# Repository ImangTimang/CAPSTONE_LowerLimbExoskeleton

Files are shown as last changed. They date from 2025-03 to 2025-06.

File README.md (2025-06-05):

# Development of a Lower Body Exoskeleton Robot

## Disclaimer
 All published here are the raw files and compilations of the drawings, schematics, programs, and design of the MEXE Capstone 1 and 2 entitled "Development of a Lower Body Exoskeleton Robot"

## Abstract
Lower-limb exoskeletons are wearable robotic systems designed to assist individuals with impairedmobility. As studies in the University solely focused on models and simulations of the lower limb. This capstone
project aims to address the gap by developing a functional prototype of a lower-body exoskeleton robot, limited on sitting and standing postures. SOLIDWORKS were used in analyzing the Adia et. al. (2022) exoskeleton
design for mechanical modeling. Design Calculations were presented by identifying the intended user’s weight and height, material selected upon the main frame and straps, Degrees of Freedom (DOF), recommended size of batteries, and gearbox development. By Fabrication methods and 3D Printing, frames were developed using Aluminum Composite Panel (ACP), Cycloidal Gearbox were printed by Polylactic Acid (PLA). Printed Circuit
Boards (PCB) were designed for the electronic schematic and integrated throughout the system. Evaluation was conducted upon indirect testing by mannequin to identify the ROM of the joints of the exoskeleton. It showed that the exoskeleton could achieve sitting and standing procedures without exceeding the ROM of the intended user.

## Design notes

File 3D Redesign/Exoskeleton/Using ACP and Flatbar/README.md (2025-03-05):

To do:
- [ ] Mechanical Stops for each joint.
- [ ] Add holes for screws, and/or bolts and nuts
- [ ] Make each part 3 layers
- [ ] Do stress analysis on each part

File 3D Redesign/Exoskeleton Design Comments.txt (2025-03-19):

Exoskeleton Design Comments

Chapter 1: 
	Intro
	 - Basically Introduce the Background, the gaps behind it and the primary general goal of the study. 
	Project Objectives
	 - Very Simple Objectives and limited objectives only.
	Scope and Limitation
	 - Defined the scope on what are the primary tasks of the project, What softwares and hardwares that will be using in this subject, what testing methods will be covered in thie project, the specific beneficiaries of the respective project.
	Importance of the Study
	 - What problems does this address to? 

Chatper 2:
	Conceptuall Literature
	 - Always dependent on the following topic involved
		 - Ang ginawa ng kuya Albert ay more on the orthosis-based robots.
			 - sa Orthosis based, may AAFO, KAFO, HAL, at BLEEX
			 - AAFO - Need of better control system and actuation system 
			 - KAFO - Nagami ng PAM
			 - HAL - This uses EMG Signals nmn
			 - BLEEX - 
	 - Purpose of Exoskeleton Robot 
		 - in Medical
		 - in Non-Medical
	 - Modes ogf the Robot Control Mechanisms
		 - Position Control
		 - Force Control
		 - Impeedance Control 
		 - 

Comments No. 1

1. Didn't define the following, sensors and actuators needed since this is only focused on the simulation of the robot
2. No involvement of the respective Inverse Kinematics of the Exoskeleton since it is too difficult to communicate
3. Since no development, only the design in being chosen
4. There is a need of comparing the simulation and the physical hardware network.
5. Kulang ng Sensors sa Previous study na involved
6 Mali ang grublers formulang ginamit
7. Alumnum 6061 ang mismong material na gamit

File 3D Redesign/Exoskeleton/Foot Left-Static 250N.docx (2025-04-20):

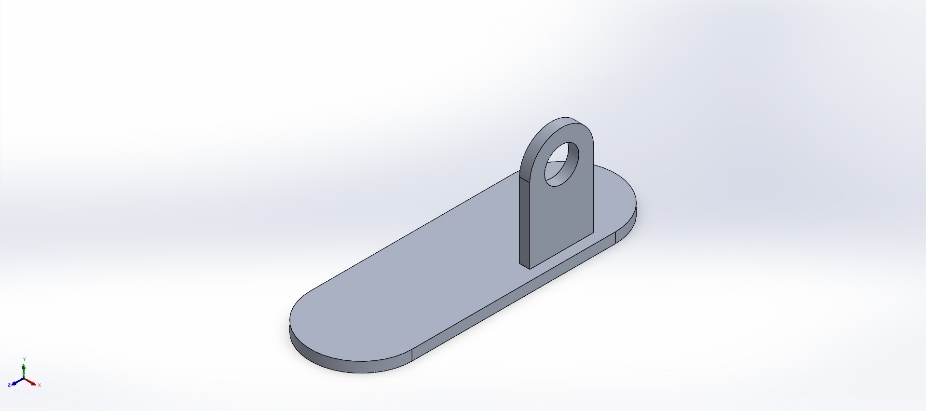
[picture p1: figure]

Simulation of Foot Left

Date: Wednesday, April 9, 2025
Designer: Solidworks

Study name: Static 1

Analysis type: Static
Description No Data

# Assumptions

# Model Information

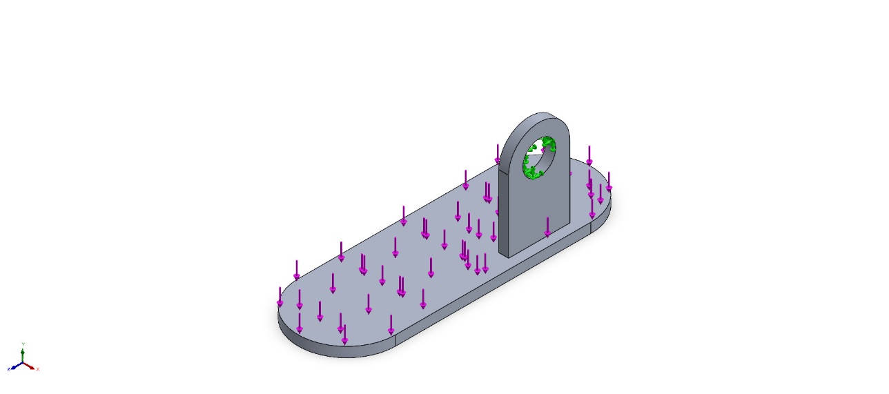
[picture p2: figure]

Model name: Foot Left

Current Configuration: Default

Solid Bodies
Document Name and Reference | Treated As | Volumetric Properties | Document Path/Date Modified

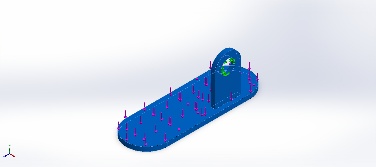
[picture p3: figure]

Cut-Extrude1 | Solid Body | Mass:0.634575 kg Volume:0.000235028 m^3 Density:2,700 kg/m^3 Weight:6.21883 N | C:\Users\allen\Documents\GitHub\CAPSTONE_LowerLimbExoskeleton\3D Redesign\Exoskeleton\Foot Left.SLDPRT Apr 6 19:37:24 2025

# Study Properties

Study name | Static 1
Analysis type | Static
Mesh type | Solid Mesh
Thermal Effect: | On
Thermal option | Include temperature loads
Zero strain temperature | 298 Kelvin
Include fluid pressure effects from SOLIDWORKS Flow Simulation | Off
Solver type | Automatic
Inplane Effect: | Off
Soft Spring: | Off
Inertial Relief: | Off
Incompatible bonding options | Automatic
Large displacement | On
Compute free body forces | On
Friction | Off
Use Adaptive Method: | Off
Result folder | SOLIDWORKS document (C:\Users\allen\Documents\GitHub\CAPSTONE_LowerLimbExoskeleton\3D Redesign\Exoskeleton)

# Units

Unit system: | SI (MKS)
Length/Displacement | mm
Temperature | Kelvin
Angular velocity | Rad/sec
Pressure/Stress | N/m^2

# Material Properties

Model Reference | Properties | Components

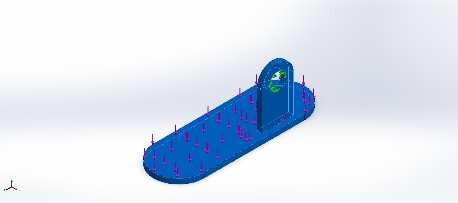
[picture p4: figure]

| Name: 6061 Alloy Model type: Linear Elastic Isotropic Default failure criterion: Max von Mises Stress Yield strength: 5.51485e+07 N/m^2 Tensile strength: 1.24084e+08 N/m^2 Elastic modulus: 6.9e+10 N/m^2 Poisson's ratio: 0.33 Mass density: 2,700 kg/m^3 Shear modulus: 2.6e+10 N/m^2 Thermal expansion coefficient: 2.4e-05 /Kelvin | SolidBody 1(Cut-Extrude1)(Foot Left)

Curve Data:N/A

# Loads and Fixtures

Fixture name | Fixture Image | Fixture Details

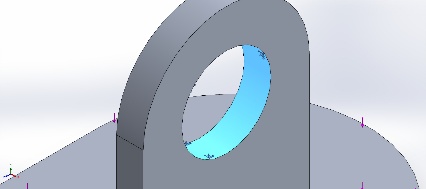
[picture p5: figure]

Fixed-1 | | Entities: 1 face(s) Type: Fixed Geometry

Resultant Forces

Components | X | Y | Z | Resultant
Reaction force(N) | -7.62939e-06 | 250 | -7.15256e-06 | 250
Reaction Moment(N.m) | 0 | 0 | 0 | 0

Load name | Load Image | Load Details

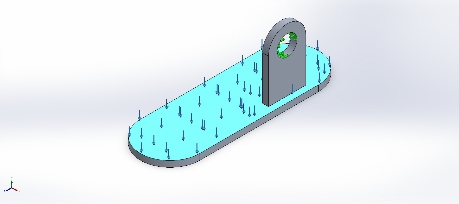
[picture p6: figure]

Force-1 | | Entities: 1 face(s) Type: Apply normal force Value: 250 N

# Connector Definitions

No Data

# Interaction Information

No Data

# Mesh information

Mesh type | Solid Mesh
Mesher Used: | Blended curvature-based mesh
Jacobian points for High quality mesh | 16 Points
Maximum element size | 6.17297 mm
Minimum element size | 6.17297 mm
Mesh Quality | High

## Mesh information - Details

Total Nodes | 17404
Total Elements | 10029
Maximum Aspect Ratio | 3.8626
% of elements with Aspect Ratio < 3 | 100
Percentage of elements with Aspect Ratio > 10 | 0
Percentage of distorted elements | 0
Time to complete mesh(hh;mm;ss): | 00:00:02
Computer name: | ENGRLEANDZ

## Mesh Quality Plots

Name | Type | Min | Max
Quality1 | Mesh | - | -

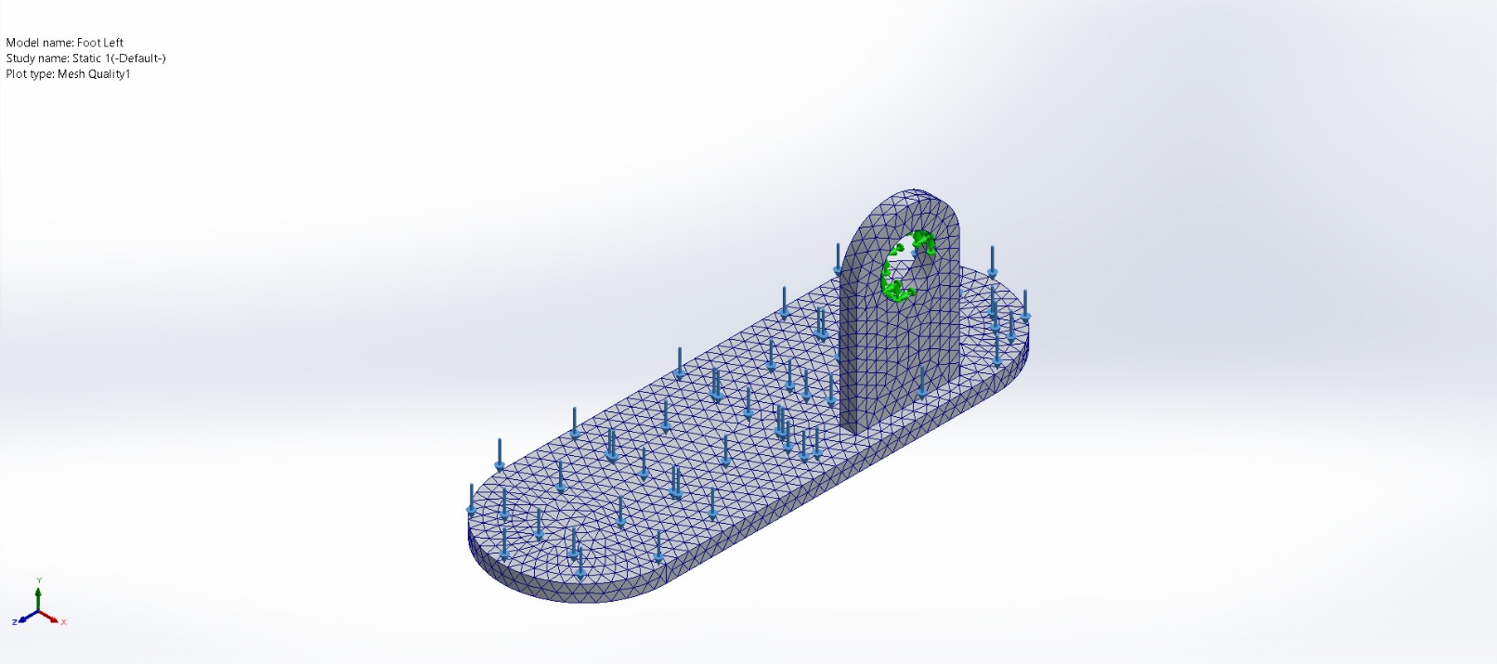
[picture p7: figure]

Foot Left-Static 1-Quality-Quality1

# Sensor Details

No Data

# Resultant Forces

## Reaction forces

Selection set | Units | Sum X | Sum Y | Sum Z | Resultant
Entire Model | N | -7.62939e-06 | 250 | -7.15256e-06 | 250

## Reaction Moments

Selection set | Units | Sum X | Sum Y | Sum Z | Resultant
Entire Model | N.m | 0 | 0 | 0 | 0

## Free body forces

Selection set | Units | Sum X | Sum Y | Sum Z | Resultant
Entire Model | N | 0 | 0 | 0 | 0

## Free body moments

Selection set | Units | Sum X | Sum Y | Sum Z | Resultant
Entire Model | N.m | 0 | 0 | 0 | 0

# Beams

No Data

# Study Results

Name | Type | Min | Max
Stress1 | VON: von Mises Stress | 7.928e+03N/m^2 Node: 2202 | 3.506e+07N/m^2 Node: 7166

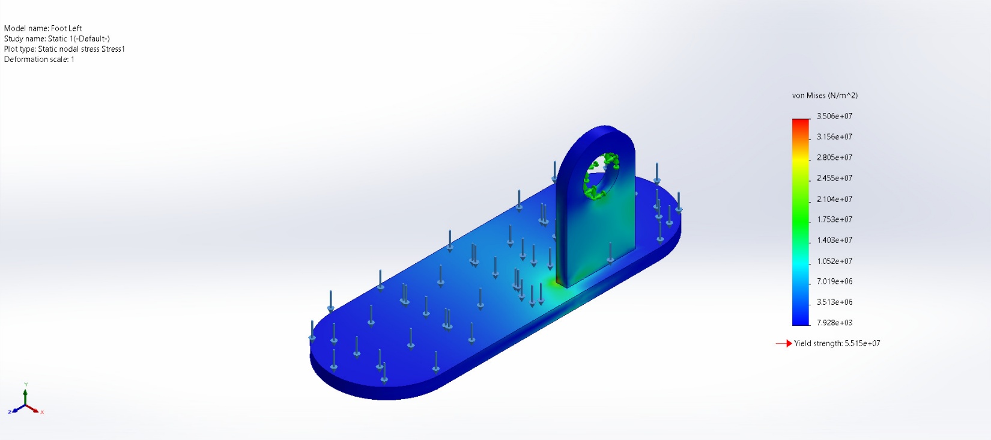
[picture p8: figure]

Foot Left-Static 1-Stress-Stress1

Name | Type | Min | Max
Displacement1 | URES: Resultant Displacement | 0.000e+00mm Node: 13 | 4.179e-01mm Node: 17183

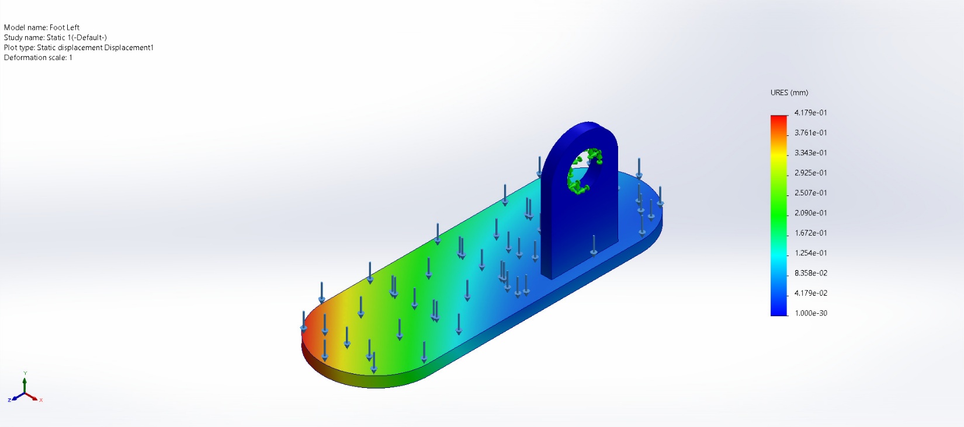
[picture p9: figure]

Foot Left-Static 1-Displacement-Displacement1

Name | Type | Min | Max
Strain1 | ESTRN: Equivalent Strain | 4.332e-07 Element: 6003 | 3.162e-04 Element: 1149

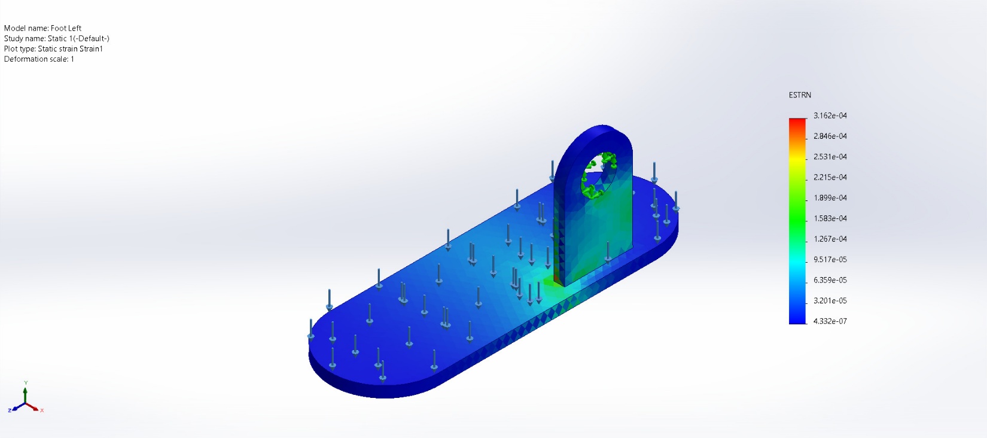
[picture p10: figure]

Foot Left-Static 1-Strain-Strain1

Name | Type
Displacement1{1} | Deformed shape

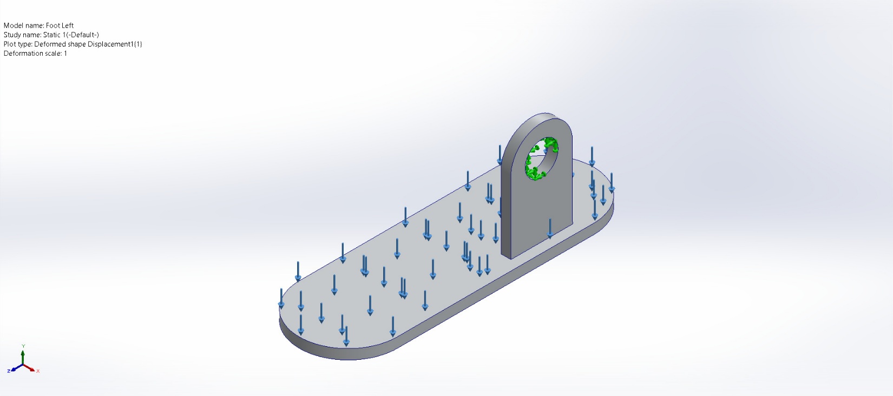
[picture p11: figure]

Foot Left-Static 1-Displacement-Displacement1{1}

# Conclusion

Analyzed with SOLIDWORKS Simulation Simulation of Foot Left 16

Analyzed with SOLIDWORKS Simulation Simulation of Foot Left 1

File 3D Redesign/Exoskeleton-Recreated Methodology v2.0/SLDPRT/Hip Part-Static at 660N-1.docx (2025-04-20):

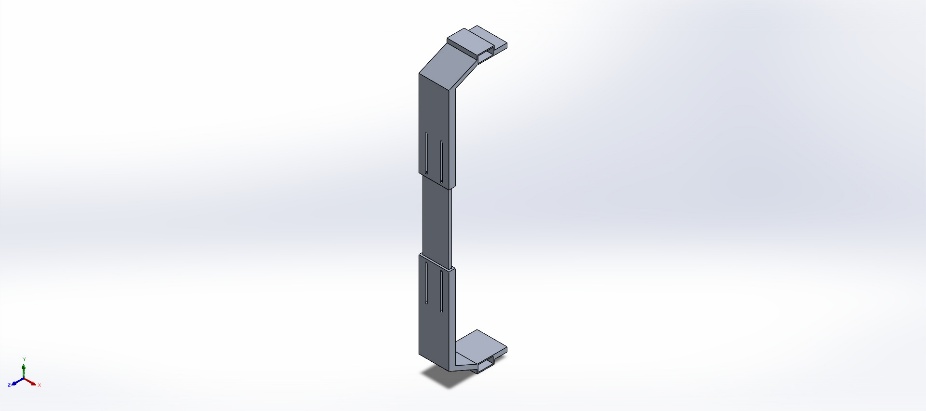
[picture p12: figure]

Simulation of Hip Part

Date: Saturday, April 12, 2025
Designer: Solidworks

Study name: Static at 660N

Analysis type: Static
Description No Data

# Assumptions

# Model Information

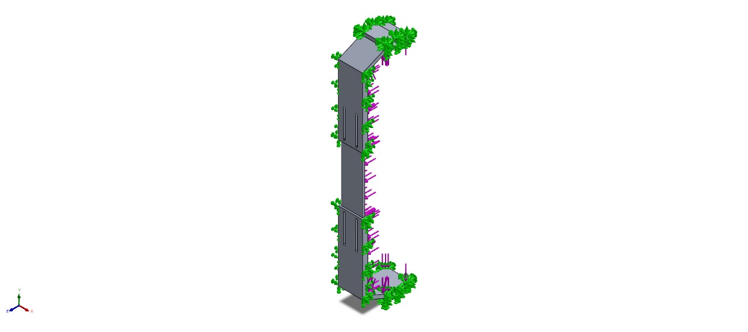
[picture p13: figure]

Model name: Hip Part

Current Configuration: Default

Solid Bodies
Document Name and Reference | Treated As | Volumetric Properties | Document Path/Date Modified

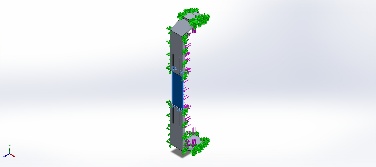
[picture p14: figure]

Revolve8 | Solid Body | Mass:0.424141 kg Volume:0.000157089 m^3 Density:2,700 kg/m^3 Weight:4.15659 N | C:\Users\allen\Documents\GitHub\CAPSTONE_LowerLimbExoskeleton\3D Redesign\Exoskeleton-Recreated Methodology v2.0\SLDPRT\Extension for Hip Part.SLDPRT Apr 12 13:36:24 2025

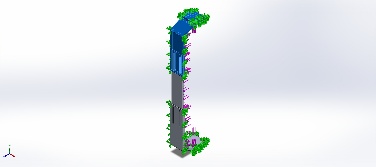
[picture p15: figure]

Cut-Extrude9 | Solid Body | Mass:1.35813 kg Volume:0.00050301 m^3 Density:2,700 kg/m^3 Weight:13.3096 N | C:\Users\allen\Documents\GitHub\CAPSTONE_LowerLimbExoskeleton\3D Redesign\Exoskeleton-Recreated Methodology v2.0\SLDPRT\Hip Part.SLDPRT Apr 12 13:36:24 2025

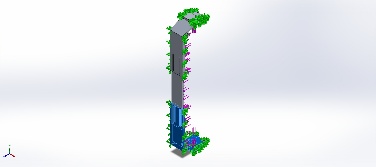
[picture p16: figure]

Cut-Extrude9 | Solid Body | Mass:1.35813 kg Volume:0.00050301 m^3 Density:2,700 kg/m^3 Weight:13.3096 N | C:\Users\allen\Documents\GitHub\CAPSTONE_LowerLimbExoskeleton\3D Redesign\Exoskeleton-Recreated Methodology v2.0\SLDPRT\Hip Part.SLDPRT Apr 12 13:36:24 2025

# Study Properties

Study name | Static at 660N
Analysis type | Static
Mesh type | Solid Mesh
Thermal Effect: | On
Thermal option | Include temperature loads
Zero strain temperature | 298 Kelvin
Include fluid pressure effects from SOLIDWORKS Flow Simulation | Off
Solver type | Automatic
Inplane Effect: | Off
Soft Spring: | Off
Inertial Relief: | Off
Incompatible bonding options | Automatic
Large displacement | Off
Compute free body forces | On
Friction | Off
Use Adaptive Method: | Off
Result folder | SOLIDWORKS document (C:\Users\allen\Documents\GitHub\CAPSTONE_LowerLimbExoskeleton\3D Redesign\Exoskeleton-Recreated Methodology v2.0\SLDPRT)

# Units

Unit system: | SI (MKS)
Length/Displacement | mm
Temperature | Kelvin
Angular velocity | Rad/sec
Pressure/Stress | N/m^2

# Material Properties

Model Reference | Properties | Components

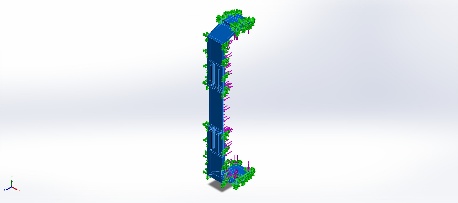
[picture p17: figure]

| Name: 6061 Alloy Model type: Linear Elastic Isotropic Default failure criterion: Max von Mises Stress Yield strength: 5.51485e+07 N/m^2 Tensile strength: 1.24084e+08 N/m^2 Elastic modulus: 6.9e+10 N/m^2 Poisson's ratio: 0.33 Mass density: 2,700 kg/m^3 Shear modulus: 2.6e+10 N/m^2 Thermal expansion coefficient: 2.4e-05 /Kelvin | SolidBody 1(Revolve8)(Extension for Hip Part-1), SolidBody 1(Cut-Extrude9)(Hip Part-1), SolidBody 1(Cut-Extrude9)(Hip Part-2)

Curve Data:N/A

# Loads and Fixtures

Fixture name | Fixture Image | Fixture Details

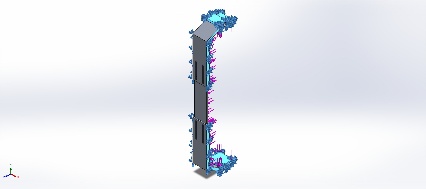
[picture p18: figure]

Fixed-1 | | Entities: 16 face(s) Type: Fixed Geometry

Resultant Forces

Components | X | Y | Z | Resultant
Reaction force(N) | 0.0299854 | -0.0656447 | -5,152.02 | 5,152.02
Reaction Moment(N.m) | 0 | 0 | 0 | 0

Load name | Load Image | Load Details

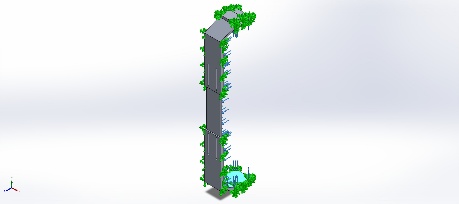
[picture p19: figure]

Force-1 | | Entities: 11 face(s) Type: Apply normal force Value: 660 N

# Connector Definitions

No Data

# Interaction Information

Interaction | Interaction Image | Interaction Properties

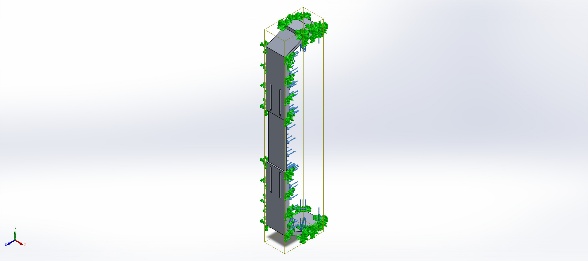
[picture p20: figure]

Global Interaction | | Type: Bonded Components: 1 component(s) Options: Independent mesh

# Mesh information

Mesh type | Solid Mesh
Mesher Used: | Blended curvature-based mesh
Jacobian points for High quality mesh | 16 Points
Maximum element size | 21.8002 mm
Minimum element size | 2.2961 mm
Mesh Quality | High
Remesh failed parts independently | Off
Reuse mesh for identical parts in an assembly (Blended curvature-based mesher only) | Off

## Mesh information - Details

Total Nodes | 21876
Total Elements | 11344
Maximum Aspect Ratio | 9.6391
% of elements with Aspect Ratio < 3 | 94.2
Percentage of elements with Aspect Ratio > 10 | 0
Percentage of distorted elements | 0
Time to complete mesh(hh;mm;ss): | 00:00:03
Computer name: | ENGRLEANDZ

## Mesh Quality Plots

Name | Type | Min | Max
Quality1 | Mesh | - | -

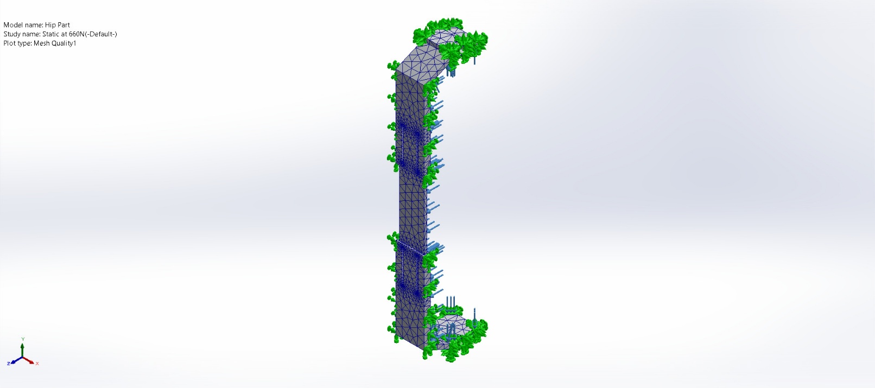
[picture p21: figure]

Hip Part-Static at 660N-Quality-Quality1

# Sensor Details

No Data

# Resultant Forces

## Reaction forces

Selection set | Units | Sum X | Sum Y | Sum Z | Resultant
Entire Model | N | 0.0299854 | -0.0656447 | -5,152.02 | 5,152.02

## Reaction Moments

Selection set | Units | Sum X | Sum Y | Sum Z | Resultant
Entire Model | N.m | 0 | 0 | 0 | 0

## Free body forces

Selection set | Units | Sum X | Sum Y | Sum Z | Resultant
Entire Model | N | 0.0414273 | -0.0985064 | 0.0857365 | 0.137005

## Free body moments

Selection set | Units | Sum X | Sum Y | Sum Z | Resultant
Entire Model | N.m | 0 | 0 | 0 | 1e-33

# Beams

No Data

# Study Results

Name | Type | Min | Max
Stress1 | VON: von Mises Stress | 0.000N/m^2 Node: 6103 | 31,833,046.000N/m^2 Node: 4836

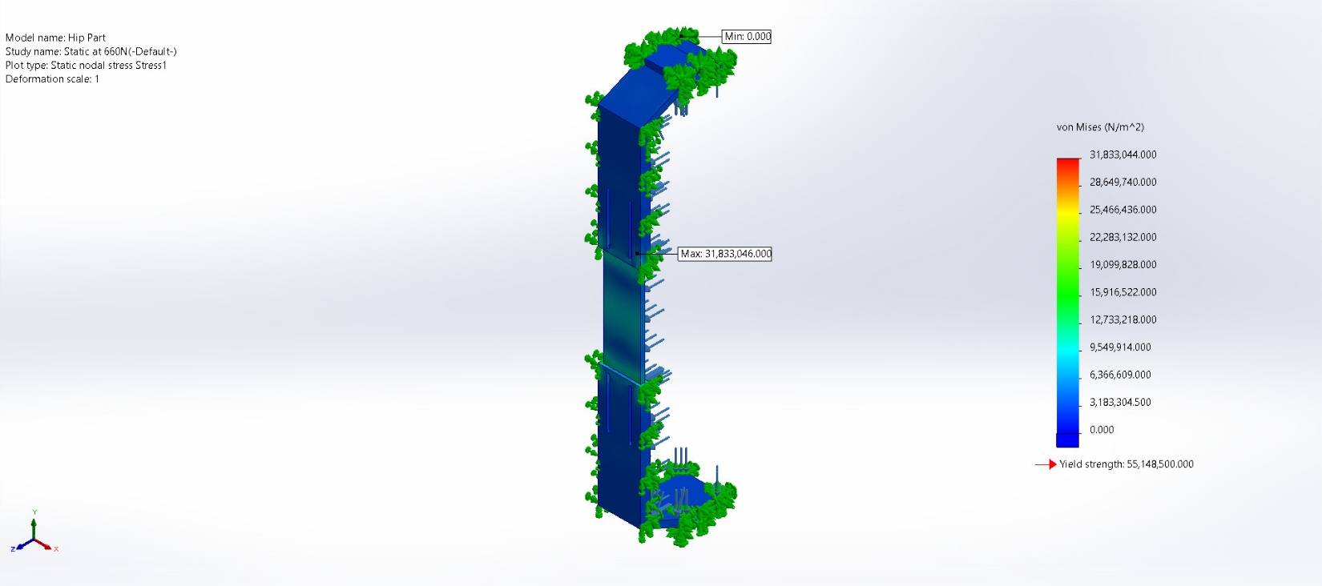
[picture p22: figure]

Hip Part-Static at 660N-Stress-Stress1

Name | Type | Min | Max
Displacement1 | URES: Resultant Displacement | 0.000e+00mm Node: 6091 | 7.067e-02mm Node: 5023

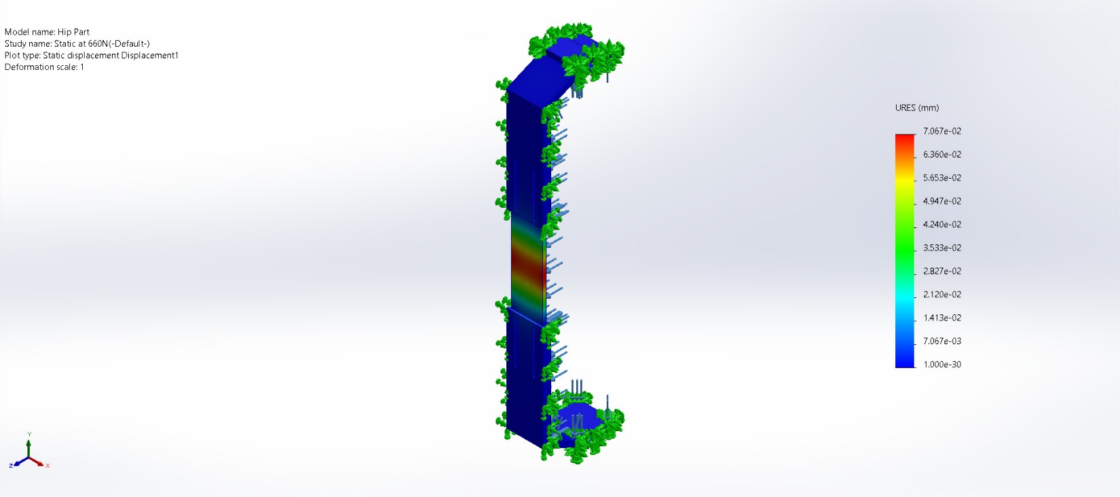
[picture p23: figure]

Hip Part-Static at 660N-Displacement-Displacement1

Name | Type | Min | Max
Strain1 | ESTRN: Equivalent Strain | 0.000e+00 Element: 4356 | 3.731e-04 Element: 2609

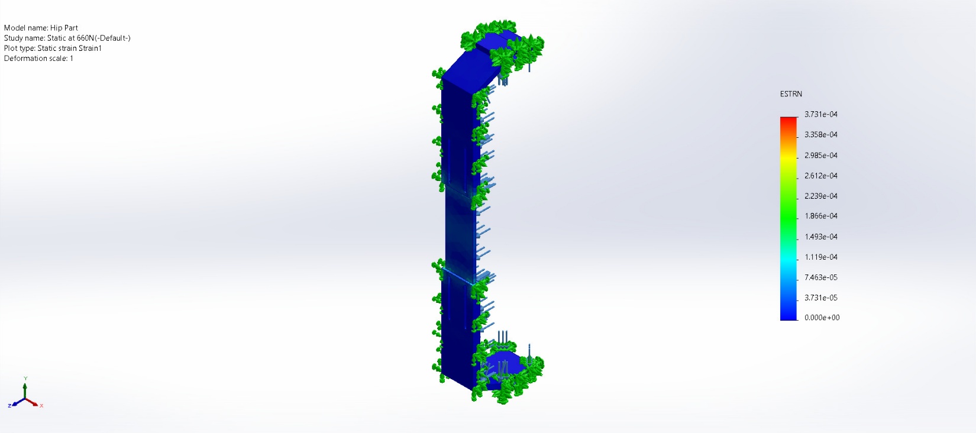
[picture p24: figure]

Hip Part-Static at 660N-Strain-Strain1

Name | Type | Min | Max
Factor of Safety1 | Max von Mises Stress | 1.732e+00 Node: 4836 | 1.000e+16 Node: 6103


Hip Part-Static at 660N-Factor of Safety-Factor of Safety1

# Conclusion

# Appendix

Analyzed with SOLIDWORKS Simulation Simulation of Hip Part 16

Analyzed with SOLIDWORKS Simulation Simulation of Hip Part 1

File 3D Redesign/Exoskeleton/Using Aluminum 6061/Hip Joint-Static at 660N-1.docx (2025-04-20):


Simulation of Hip Joint

Date: Saturday, March 15, 2025
Designer: Solidworks

Study name: Static at 660N

Analysis type: Static
Description No Data

# Assumptions

# Model Information


Model name: Hip Joint

Current Configuration: Default

Solid Bodies
Document Name and Reference | Treated As | Volumetric Properties | Document Path/Date Modified


CSK for M6 Countersunk Flat Head Screw1 | Solid Body | Mass:0.28663 kg Volume:0.000106159 m^3 Density:2,700 kg/m^3 Weight:2.80897 N | C:\Users\allen\Downloads\CAPSTONE_LowerLimbExoskeleton-main\CAPSTONE_LowerLimbExoskeleton-main\3D Redesign\Exoskeleton\Using Aluminum 6061\Hip Joint.SLDPRT Mar 15 09:49:36 2025

# Study Properties

Study name | Static at 660N
Analysis type | Static
Mesh type | Solid Mesh
Thermal Effect: | On
Thermal option | Include temperature loads
Zero strain temperature | 298 Kelvin
Include fluid pressure effects from SOLIDWORKS Flow Simulation | Off
Solver type | Automatic
Inplane Effect: | Off
Soft Spring: | Off
Inertial Relief: | Off
Incompatible bonding options | Automatic
Large displacement | Off
Compute free body forces | On
Friction | Off
Use Adaptive Method: | Off
Result folder | SOLIDWORKS document (C:\Users\allen\Downloads\CAPSTONE_LowerLimbExoskeleton-main\CAPSTONE_LowerLimbExoskeleton-main\3D Redesign\Exoskeleton\Using Aluminum 6061)

# Units

Unit system: | SI (MKS)
Length/Displacement | mm
Temperature | Kelvin
Angular velocity | Rad/sec
Pressure/Stress | N/m^2

# Material Properties

Model Reference | Properties | Components


| Name: 6061 Alloy Model type: Linear Elastic Isotropic Default failure criterion: Unknown Yield strength: 5.51485e+07 N/m^2 Tensile strength: 1.24084e+08 N/m^2 Elastic modulus: 6.9e+10 N/m^2 Poisson's ratio: 0.33 Mass density: 2,700 kg/m^3 Shear modulus: 2.6e+10 N/m^2 Thermal expansion coefficient: 2.4e-05 /Kelvin | SolidBody 1(CSK for M6 Countersunk Flat Head Screw1)(Hip Joint)

Curve Data:N/A

# Loads and Fixtures

Fixture name | Fixture Image | Fixture Details


Fixed-1 | | Entities: 12 face(s) Type: Fixed Geometry

Resultant Forces

Components | X | Y | Z | Resultant
Reaction force(N) | 660.001 | -0.000192523 | 0.00113624 | 660.001
Reaction Moment(N.m) | 0 | 0 | 0 | 0

Load name | Load Image | Load Details


Force-1 | | Entities: 1 face(s) Type: Apply normal force Value: 660 N

# Connector Definitions

No Data

# Interaction Information

No Data

# Mesh information

Mesh type | Solid Mesh
Mesher Used: | Blended curvature-based mesh
Jacobian points for High quality mesh | 16 Points
Maximum element size | 4.73643 mm
Minimum element size | 1.5788 mm
Mesh Quality | High

## Mesh information - Details

Total Nodes | 18393
Total Elements | 10858
Maximum Aspect Ratio | 7.5923
% of elements with Aspect Ratio < 3 | 99.3
Percentage of elements with Aspect Ratio > 10 | 0
Percentage of distorted elements | 0
Time to complete mesh(hh;mm;ss): | 00:00:03
Computer name: | ENGRLEANDZ

## Mesh Quality Plots

Name | Type | Min | Max
Quality1 | Mesh | - | -


Hip Joint-Static at 660N-Quality-Quality1

# Sensor Details

No Data

# Resultant Forces

## Reaction forces

Selection set | Units | Sum X | Sum Y | Sum Z | Resultant
Entire Model | N | 660.001 | -0.000192523 | 0.00113624 | 660.001

## Reaction Moments

Selection set | Units | Sum X | Sum Y | Sum Z | Resultant
Entire Model | N.m | 0 | 0 | 0 | 0

## Free body forces

Selection set | Units | Sum X | Sum Y | Sum Z | Resultant
Entire Model | N | 0.000485837 | 0.0024581 | 0.00139342 | 0.00286703

## Free body moments

Selection set | Units | Sum X | Sum Y | Sum Z | Resultant
Entire Model | N.m | 0 | 0 | 0 | 1e-33

# Beams

No Data

# Study Results

Name | Type | Min | Max
Stress1 | VON: von Mises Stress | 0.005N/m^2 Node: 56 | 1,649,803.250N/m^2 Node: 17588


Hip Joint-Static at 660N-Stress-Stress1

Name | Type | Min | Max
Displacement1 | URES: Resultant Displacement | 0.000e+00mm Node: 1 | 2.061e-04mm Node: 14168


Hip Joint-Static at 660N-Displacement-Displacement1

Name | Type | Min | Max
Strain1 | ESTRN: Equivalent Strain | 2.195e-07 Element: 1624 | 1.098e-05 Element: 7942


Hip Joint-Static at 660N-Strain-Strain1

Name | Type
Displacement1{1} | Deformed shape


Hip Joint-Static at 660N-Displacement-Displacement1{1}

# Conclusion

Analyzed with SOLIDWORKS Simulation Simulation of Hip Joint 16

Analyzed with SOLIDWORKS Simulation Simulation of Hip Joint 1

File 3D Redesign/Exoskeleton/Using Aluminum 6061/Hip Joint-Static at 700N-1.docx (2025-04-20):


Simulation of Hip Joint

Date: Saturday, March 15, 2025
Designer: Solidworks

Study name: Static at 700N

Analysis type: Static
Description No Data

# Assumptions

# Model Information


Model name: Hip Joint

Current Configuration: Default

Solid Bodies
Document Name and Reference | Treated As | Volumetric Properties | Document Path/Date Modified


CSK for M6 Countersunk Flat Head Screw1 | Solid Body | Mass:0.28663 kg Volume:0.000106159 m^3 Density:2,700 kg/m^3 Weight:2.80897 N | C:\Users\allen\Downloads\CAPSTONE_LowerLimbExoskeleton-main\CAPSTONE_LowerLimbExoskeleton-main\3D Redesign\Exoskeleton\Using Aluminum 6061\Hip Joint.SLDPRT Mar 15 09:49:36 2025

# Study Properties

Study name | Static at 700N
Analysis type | Static
Mesh type | Solid Mesh
Thermal Effect: | On
Thermal option | Include temperature loads
Zero strain temperature | 298 Kelvin
Include fluid pressure effects from SOLIDWORKS Flow Simulation | Off
Solver type | Automatic
Inplane Effect: | Off
Soft Spring: | Off
Inertial Relief: | Off
Incompatible bonding options | Automatic
Large displacement | Off
Compute free body forces | On
Friction | Off
Use Adaptive Method: | Off
Result folder | SOLIDWORKS document (C:\Users\allen\Downloads\CAPSTONE_LowerLimbExoskeleton-main\CAPSTONE_LowerLimbExoskeleton-main\3D Redesign\Exoskeleton\Using Aluminum 6061)

# Units

Unit system: | SI (MKS)
Length/Displacement | mm
Temperature | Kelvin
Angular velocity | Rad/sec
Pressure/Stress | N/m^2

# Material Properties

Model Reference | Properties | Components


| Name: 6061 Alloy Model type: Linear Elastic Isotropic Default failure criterion: Unknown Yield strength: 5.51485e+07 N/m^2 Tensile strength: 1.24084e+08 N/m^2 Elastic modulus: 6.9e+10 N/m^2 Poisson's ratio: 0.33 Mass density: 2,700 kg/m^3 Shear modulus: 2.6e+10 N/m^2 Thermal expansion coefficient: 2.4e-05 /Kelvin | SolidBody 1(CSK for M6 Countersunk Flat Head Screw1)(Hip Joint)

Curve Data:N/A

# Loads and Fixtures

Fixture name | Fixture Image | Fixture Details


Fixed-1 | | Entities: 12 face(s) Type: Fixed Geometry

Resultant Forces

Components | X | Y | Z | Resultant
Reaction force(N) | -700 | 0.000115871 | -0.00144973 | 700
Reaction Moment(N.m) | 0 | 0 | 0 | 0

Load name | Load Image | Load Details


Force-1 | | Entities: 1 face(s) Type: Apply normal force Value: 700 N

# Connector Definitions

No Data

# Interaction Information

No Data

# Mesh information

Mesh type | Solid Mesh
Mesher Used: | Blended curvature-based mesh
Jacobian points for High quality mesh | 16 Points
Maximum element size | 4.73643 mm
Minimum element size | 1.5788 mm
Mesh Quality | High

## Mesh information - Details

Total Nodes | 18393
Total Elements | 10858
Maximum Aspect Ratio | 7.5923
% of elements with Aspect Ratio < 3 | 99.3
Percentage of elements with Aspect Ratio > 10 | 0
Percentage of distorted elements | 0
Time to complete mesh(hh;mm;ss): | 00:00:02
Computer name: | ENGRLEANDZ

## Mesh Quality Plots

Name | Type | Min | Max
Quality1 | Mesh | - | -


Hip Joint-Static at 700N-Quality-Quality1

# Sensor Details

No Data

# Resultant Forces

## Reaction forces

Selection set | Units | Sum X | Sum Y | Sum Z | Resultant
Entire Model | N | -700 | 0.000115871 | -0.00144973 | 700

## Reaction Moments

Selection set | Units | Sum X | Sum Y | Sum Z | Resultant
Entire Model | N.m | 0 | 0 | 0 | 0

## Free body forces

Selection set | Units | Sum X | Sum Y | Sum Z | Resultant
Entire Model | N | 0.0019682 | -0.00308537 | -0.00252546 | 0.0044465

## Free body moments

Selection set | Units | Sum X | Sum Y | Sum Z | Resultant
Entire Model | N.m | 0 | 0 | 0 | 1e-33

# Beams

No Data

# Study Results

Name | Type | Min | Max
Stress1 | VON: von Mises Stress | 0.005N/m^2 Node: 53 | 1,720,823.250N/m^2 Node: 17588


Hip Joint-Static at 700N-Stress-Stress1

Name | Type | Min | Max
Displacement1 | URES: Resultant Displacement | 0.000e+00mm Node: 1 | 2.096e-04mm Node: 354


Hip Joint-Static at 700N-Displacement-Displacement1

Name | Type | Min | Max
Strain1 | ESTRN: Equivalent Strain | 2.718e-07 Element: 4901 | 1.159e-05 Element: 9477


Hip Joint-Static at 700N-Strain-Strain1

Name | Type
Displacement1{1} | Deformed shape


Hip Joint-Static at 700N-Displacement-Displacement1{1}

# Conclusion

Analyzed with SOLIDWORKS Simulation Simulation of Hip Joint 16

Analyzed with SOLIDWORKS Simulation Simulation of Hip Joint 1

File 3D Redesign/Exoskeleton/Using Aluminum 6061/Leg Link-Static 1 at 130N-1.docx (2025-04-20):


Simulation of Leg Link

Date: Saturday, March 15, 2025
Designer: Solidworks

Study name: Static 1 at 130N

Analysis type: Static
Description No Data

# Assumptions

# Model Information


Model name: Leg Link

Current Configuration: Default

Solid Bodies
Document Name and Reference | Treated As | Volumetric Properties | Document Path/Date Modified


Boss-Extrude1 | Solid Body | Mass:0.568126 kg Volume:0.000210417 m^3 Density:2,700 kg/m^3 Weight:5.56763 N | C:\Users\allen\Downloads\CAPSTONE_LowerLimbExoskeleton-main\CAPSTONE_LowerLimbExoskeleton-main\3D Redesign\Exoskeleton\Using Aluminum 6061\Leg Link.SLDPRT Mar 15 10:00:20 2025

# Study Properties

Study name | Static 1 at 130N
Analysis type | Static
Mesh type | Solid Mesh
Thermal Effect: | On
Thermal option | Include temperature loads
Zero strain temperature | 298 Kelvin
Include fluid pressure effects from SOLIDWORKS Flow Simulation | Off
Solver type | Automatic
Inplane Effect: | Off
Soft Spring: | Off
Inertial Relief: | Off
Incompatible bonding options | Automatic
Large displacement | Off
Compute free body forces | On
Friction | Off
Use Adaptive Method: | Off
Result folder | SOLIDWORKS document (C:\Users\allen\Downloads\CAPSTONE_LowerLimbExoskeleton-main\CAPSTONE_LowerLimbExoskeleton-main\3D Redesign\Exoskeleton\Using Aluminum 6061)

# Units

Unit system: | SI (MKS)
Length/Displacement | mm
Temperature | Kelvin
Angular velocity | Rad/sec
Pressure/Stress | N/m^2

# Material Properties

Model Reference | Properties | Components


| Name: 6061 Alloy Model type: Linear Elastic Isotropic Default failure criterion: Unknown Yield strength: 5.51485e+07 N/m^2 Tensile strength: 1.24084e+08 N/m^2 Elastic modulus: 6.9e+10 N/m^2 Poisson's ratio: 0.33 Mass density: 2,700 kg/m^3 Shear modulus: 2.6e+10 N/m^2 Thermal expansion coefficient: 2.4e-05 /Kelvin | SolidBody 1(Boss-Extrude1)(Leg Link)

Curve Data:N/A

# Loads and Fixtures

Fixture name | Fixture Image | Fixture Details


Fixed-1 | | Entities: 3 face(s) Type: Fixed Geometry

Resultant Forces

Components | X | Y | Z | Resultant
Reaction force(N) | 75.6218 | -0.460763 | 0.00058794 | 75.6232
Reaction Moment(N.m) | 0 | 0 | 0 | 0


Fixed-2 | | Entities: 2 face(s) Type: Fixed Geometry

Resultant Forces

Components | X | Y | Z | Resultant
Reaction force(N) | 54.3774 | 0.463641 | -0.00729361 | 54.3794
Reaction Moment(N.m) | 0 | 0 | 0 | 0

Load name | Load Image | Load Details


Force-1 | | Entities: 1 face(s) Type: Apply normal force Value: 130 N

# Connector Definitions

No Data

# Interaction Information

No Data

# Mesh information

Mesh type | Solid Mesh
Mesher Used: | Blended curvature-based mesh
Jacobian points for High quality mesh | 16 Points
Maximum element size | 5.94953 mm
Minimum element size | 5.94953 mm
Mesh Quality | High

## Mesh information - Details

Total Nodes | 17232
Total Elements | 9847
Maximum Aspect Ratio | 2.9278
% of elements with Aspect Ratio < 3 | 100
Percentage of elements with Aspect Ratio > 10 | 0
Percentage of distorted elements | 0
Time to complete mesh(hh;mm;ss): | 00:00:02
Computer name: | ENGRLEANDZ

## Mesh Quality Plots

Name | Type | Min | Max
Quality1 | Mesh | - | -


Leg Link-Static 1 at 130N-Quality-Quality1

# Sensor Details

No Data

# Resultant Forces

## Reaction forces

Selection set | Units | Sum X | Sum Y | Sum Z | Resultant
Entire Model | N | 129.999 | 0.00287151 | -0.00670385 | 129.999

## Reaction Moments

Selection set | Units | Sum X | Sum Y | Sum Z | Resultant
Entire Model | N.m | 0 | 0 | 0 | 0

## Free body forces

Selection set | Units | Sum X | Sum Y | Sum Z | Resultant
Entire Model | N | 0.00618643 | 0.0132044 | 0.00813296 | 0.0166965

## Free body moments

Selection set | Units | Sum X | Sum Y | Sum Z | Resultant
Entire Model | N.m | 0 | 0 | 0 | 1e-33

# Beams

No Data

# Study Results

Name | Type | Min | Max
Stress1 | VON: von Mises Stress | 856.969N/m^2 Node: 13043 | 5,401,845.500N/m^2 Node: 6822


Leg Link-Static 1 at 130N-Stress-Stress1

Name | Type | Min | Max
Displacement1 | URES: Resultant Displacement | 0.000e+00mm Node: 2 | 5.472e-02mm Node: 3258


Leg Link-Static 1 at 130N-Displacement-Displacement1

Name | Type | Min | Max
Strain1 | ESTRN: Equivalent Strain | 1.466e-08 Element: 4679 | 5.670e-05 Element: 8249


Leg Link-Static 1 at 130N-Strain-Strain1

# Conclusion

Analyzed with SOLIDWORKS Simulation Simulation of Leg Link 16

Analyzed with SOLIDWORKS Simulation Simulation of Leg Link 1

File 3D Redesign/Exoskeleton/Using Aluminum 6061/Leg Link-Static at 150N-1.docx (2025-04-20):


Simulation of Leg Link

Date: Saturday, March 15, 2025
Designer: Solidworks

Study name: Static at 150N

Analysis type: Static
Description No Data

# Assumptions

# Model Information


Model name: Leg Link

Current Configuration: Default

Solid Bodies
Document Name and Reference | Treated As | Volumetric Properties | Document Path/Date Modified


Boss-Extrude1 | Solid Body | Mass:0.568126 kg Volume:0.000210417 m^3 Density:2,700 kg/m^3 Weight:5.56763 N | C:\Users\allen\Downloads\CAPSTONE_LowerLimbExoskeleton-main\CAPSTONE_LowerLimbExoskeleton-main\3D Redesign\Exoskeleton\Using Aluminum 6061\Leg Link.SLDPRT Mar 15 10:00:20 2025

# Study Properties

Study name | Static at 150N
Analysis type | Static
Mesh type | Solid Mesh
Thermal Effect: | On
Thermal option | Include temperature loads
Zero strain temperature | 298 Kelvin
Include fluid pressure effects from SOLIDWORKS Flow Simulation | Off
Solver type | Automatic
Inplane Effect: | Off
Soft Spring: | Off
Inertial Relief: | Off
Incompatible bonding options | Automatic
Large displacement | Off
Compute free body forces | On
Friction | Off
Use Adaptive Method: | Off
Result folder | SOLIDWORKS document (C:\Users\allen\Downloads\CAPSTONE_LowerLimbExoskeleton-main\CAPSTONE_LowerLimbExoskeleton-main\3D Redesign\Exoskeleton\Using Aluminum 6061)

# Units

Unit system: | SI (MKS)
Length/Displacement | mm
Temperature | Kelvin
Angular velocity | Rad/sec
Pressure/Stress | N/m^2

# Material Properties

Model Reference | Properties | Components


| Name: 6061 Alloy Model type: Linear Elastic Isotropic Default failure criterion: Unknown Yield strength: 5.51485e+07 N/m^2 Tensile strength: 1.24084e+08 N/m^2 Elastic modulus: 6.9e+10 N/m^2 Poisson's ratio: 0.33 Mass density: 2,700 kg/m^3 Shear modulus: 2.6e+10 N/m^2 Thermal expansion coefficient: 2.4e-05 /Kelvin | SolidBody 1(Boss-Extrude1)(Leg Link)

Curve Data:N/A

# Loads and Fixtures

Fixture name | Fixture Image | Fixture Details


Fixed-1 | | Entities: 3 face(s) Type: Fixed Geometry

Resultant Forces

Components | X | Y | Z | Resultant
Reaction force(N) | 87.2559 | -0.531641 | 0.000676155 | 87.2576
Reaction Moment(N.m) | 0 | 0 | 0 | 0


Fixed-2 | | Entities: 2 face(s) Type: Fixed Geometry

Resultant Forces

Components | X | Y | Z | Resultant
Reaction force(N) | 62.7432 | 0.53496 | -0.0084165 | 62.7454
Reaction Moment(N.m) | 0 | 0 | 0 | 0

Load name | Load Image | Load Details


Force-1 | | Entities: 1 face(s) Type: Apply normal force Value: 150 N

# Connector Definitions

No Data

# Interaction Information

No Data

# Mesh information

Mesh type | Solid Mesh
Mesher Used: | Blended curvature-based mesh
Jacobian points for High quality mesh | 16 Points
Maximum element size | 5.94953 mm
Minimum element size | 5.94953 mm
Mesh Quality | High

## Mesh information - Details

Total Nodes | 17232
Total Elements | 9847
Maximum Aspect Ratio | 2.9278
% of elements with Aspect Ratio < 3 | 100
Percentage of elements with Aspect Ratio > 10 | 0
Percentage of distorted elements | 0
Time to complete mesh(hh;mm;ss): | 00:00:02
Computer name: | ENGRLEANDZ

## Mesh Quality Plots

Name | Type | Min | Max
Quality1 | Mesh | - | -


Leg Link-Static at 150N-Quality-Quality1

# Sensor Details

No Data

# Resultant Forces

## Reaction forces

Selection set | Units | Sum X | Sum Y | Sum Z | Resultant
Entire Model | N | 149.999 | 0.00330544 | -0.00772095 | 149.999

## Reaction Moments

Selection set | Units | Sum X | Sum Y | Sum Z | Resultant
Entire Model | N.m | 0 | 0 | 0 | 0

## Free body forces

Selection set | Units | Sum X | Sum Y | Sum Z | Resultant
Entire Model | N | 0.00710532 | 0.0152327 | 0.00938237 | 0.0192496

## Free body moments

Selection set | Units | Sum X | Sum Y | Sum Z | Resultant
Entire Model | N.m | 0 | 0 | 0 | 1e-33

# Beams

No Data

# Study Results

Name | Type | Min | Max
Stress1 | VON: von Mises Stress | 988.810N/m^2 Node: 13043 | 6,232,898.000N/m^2 Node: 6822


Leg Link-Static at 150N-Stress-Stress1

Name | Type | Min | Max
Displacement1 | URES: Resultant Displacement | 0.000e+00mm Node: 2 | 6.314e-02mm Node: 3258


Leg Link-Static at 150N-Displacement-Displacement1

Name | Type | Min | Max
Strain1 | ESTRN: Equivalent Strain | 1.691e-08 Element: 4679 | 6.542e-05 Element: 8249


Leg Link-Static at 150N-Strain-Strain1

# Conclusion

Analyzed with SOLIDWORKS Simulation Simulation of Leg Link 16

Analyzed with SOLIDWORKS Simulation Simulation of Leg Link 1

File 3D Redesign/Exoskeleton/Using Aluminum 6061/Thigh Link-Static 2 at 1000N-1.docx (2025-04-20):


Simulation of Thigh Link

Date: Saturday, March 15, 2025
Designer: Solidworks

Study name: Static 2 at 1000N

Analysis type: Static
Description No Data

# Assumptions

# Model Information


Model name: Thigh Link

Current Configuration: Default

Solid Bodies
Document Name and Reference | Treated As | Volumetric Properties | Document Path/Date Modified


CSK for M6 Countersunk Flat Head Screw1 | Solid Body | Mass:0.71216 kg Volume:0.000263763 m^3 Density:2,700 kg/m^3 Weight:6.97917 N | C:\Users\allen\Downloads\CAPSTONE_LowerLimbExoskeleton-main\CAPSTONE_LowerLimbExoskeleton-main\3D Redesign\Exoskeleton\Using Aluminum 6061\Thigh Link.SLDPRT Mar 15 10:02:15 2025

# Study Properties

Study name | Static 2 at 1000N
Analysis type | Static
Mesh type | Solid Mesh
Thermal Effect: | On
Thermal option | Include temperature loads
Zero strain temperature | 298 Kelvin
Include fluid pressure effects from SOLIDWORKS Flow Simulation | Off
Solver type | Automatic
Inplane Effect: | Off
Soft Spring: | Off
Inertial Relief: | Off
Incompatible bonding options | Automatic
Large displacement | Off
Compute free body forces | On
Friction | Off
Use Adaptive Method: | Off
Result folder | SOLIDWORKS document (C:\Users\allen\Downloads\CAPSTONE_LowerLimbExoskeleton-main\CAPSTONE_LowerLimbExoskeleton-main\3D Redesign\Exoskeleton\Using Aluminum 6061)

# Units

Unit system: | SI (MKS)
Length/Displacement | mm
Temperature | Kelvin
Angular velocity | Rad/sec
Pressure/Stress | N/m^2

# Material Properties

Model Reference | Properties | Components


| Name: 6061 Alloy Model type: Linear Elastic Isotropic Default failure criterion: Unknown Yield strength: 5.51485e+07 N/m^2 Tensile strength: 1.24084e+08 N/m^2 Elastic modulus: 6.9e+10 N/m^2 Poisson's ratio: 0.33 Mass density: 2,700 kg/m^3 Shear modulus: 2.6e+10 N/m^2 Thermal expansion coefficient: 2.4e-05 /Kelvin | SolidBody 1(CSK for M6 Countersunk Flat Head Screw1)(Thigh Link)

Curve Data:N/A

# Loads and Fixtures

Fixture name | Fixture Image | Fixture Details


Fixed-1 | | Entities: 15 face(s) Type: Fixed Geometry

Resultant Forces

Components | X | Y | Z | Resultant
Reaction force(N) | -1,000.02 | 0.00565845 | -0.0138128 | 1,000.02
Reaction Moment(N.m) | 0 | 0 | 0 | 0

Load name | Load Image | Load Details


Force-1 | | Entities: 1 face(s) Type: Apply normal force Value: 1,000 N

# Connector Definitions

No Data

# Interaction Information

No Data

# Mesh information

Mesh type | Solid Mesh
Mesher Used: | Blended curvature-based mesh
Jacobian points for High quality mesh | 16 Points
Maximum element size | 6.41491 mm
Minimum element size | 2.13828 mm
Mesh Quality | High

## Mesh information - Details

Total Nodes | 21646
Total Elements | 12279
Maximum Aspect Ratio | 6.458
% of elements with Aspect Ratio < 3 | 99.5
Percentage of elements with Aspect Ratio > 10 | 0
Percentage of distorted elements | 0
Time to complete mesh(hh;mm;ss): | 00:00:02
Computer name: | ENGRLEANDZ

## Mesh Quality Plots

Name | Type | Min | Max
Quality1 | Mesh | - | -


Thigh Link-Static 2 at 1000N-Quality-Quality1

# Sensor Details

No Data

# Resultant Forces

## Reaction forces

Selection set | Units | Sum X | Sum Y | Sum Z | Resultant
Entire Model | N | -1,000.02 | 0.00565845 | -0.0138128 | 1,000.02

## Reaction Moments

Selection set | Units | Sum X | Sum Y | Sum Z | Resultant
Entire Model | N.m | 0 | 0 | 0 | 0

## Free body forces

Selection set | Units | Sum X | Sum Y | Sum Z | Resultant
Entire Model | N | -0.00261902 | 0.0721005 | -0.0403229 | 0.0826515

## Free body moments

Selection set | Units | Sum X | Sum Y | Sum Z | Resultant
Entire Model | N.m | 0 | 0 | 0 | 1e-33

# Beams

No Data

# Study Results

Name | Type | Min | Max
Stress1 | VON: von Mises Stress | 304.340N/m^2 Node: 18226 | 47,958,568.000N/m^2 Node: 20430


Thigh Link-Static 2 at 1000N-Stress-Stress1

Name | Type | Min | Max
Displacement1 | URES: Resultant Displacement | 0.000e+00mm Node: 1 | 1.606e-01mm Node: 20783


Thigh Link-Static 2 at 1000N-Displacement-Displacement1

Name | Type | Min | Max
Strain1 | ESTRN: Equivalent Strain | 4.410e-08 Element: 8823 | 4.374e-04 Element: 8144


Thigh Link-Static 2 at 1000N-Strain-Strain1

Name | Type
Displacement1{1} | URES: Resultant Displacement


Thigh Link-Static 2 at 1000N-Displacement-Displacement1{1}

# Conclusion

Analyzed with SOLIDWORKS Simulation Simulation of Thigh Link 16

Analyzed with SOLIDWORKS Simulation Simulation of Thigh Link 1

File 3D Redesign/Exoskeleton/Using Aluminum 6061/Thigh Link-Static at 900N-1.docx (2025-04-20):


Simulation of Thigh Link

Date: Saturday, March 15, 2025
Designer: Solidworks

Study name: Static at 900N

Analysis type: Static
Description No Data

# Assumptions

# Model Information


Model name: Thigh Link

Current Configuration: Default

Solid Bodies
Document Name and Reference | Treated As | Volumetric Properties | Document Path/Date Modified


CSK for M6 Countersunk Flat Head Screw1 | Solid Body | Mass:0.71216 kg Volume:0.000263763 m^3 Density:2,700 kg/m^3 Weight:6.97917 N | C:\Users\allen\Downloads\CAPSTONE_LowerLimbExoskeleton-main\CAPSTONE_LowerLimbExoskeleton-main\3D Redesign\Exoskeleton\Using Aluminum 6061\Thigh Link.SLDPRT Mar 15 10:02:15 2025

# Study Properties

Study name | Static at 900N
Analysis type | Static
Mesh type | Solid Mesh
Thermal Effect: | On
Thermal option | Include temperature loads
Zero strain temperature | 298 Kelvin
Include fluid pressure effects from SOLIDWORKS Flow Simulation | Off
Solver type | Automatic
Inplane Effect: | Off
Soft Spring: | Off
Inertial Relief: | Off
Incompatible bonding options | Automatic
Large displacement | Off
Compute free body forces | On
Friction | Off
Use Adaptive Method: | Off
Result folder | SOLIDWORKS document (C:\Users\allen\Downloads\CAPSTONE_LowerLimbExoskeleton-main\CAPSTONE_LowerLimbExoskeleton-main\3D Redesign\Exoskeleton\Using Aluminum 6061)

# Units

Unit system: | SI (MKS)
Length/Displacement | mm
Temperature | Kelvin
Angular velocity | Rad/sec
Pressure/Stress | N/m^2

# Material Properties

Model Reference | Properties | Components


| Name: 6061 Alloy Model type: Linear Elastic Isotropic Default failure criterion: Unknown Yield strength: 5.51485e+07 N/m^2 Tensile strength: 1.24084e+08 N/m^2 Elastic modulus: 6.9e+10 N/m^2 Poisson's ratio: 0.33 Mass density: 2,700 kg/m^3 Shear modulus: 2.6e+10 N/m^2 Thermal expansion coefficient: 2.4e-05 /Kelvin | SolidBody 1(CSK for M6 Countersunk Flat Head Screw1)(Thigh Link)

Curve Data:N/A

# Loads and Fixtures

Fixture name | Fixture Image | Fixture Details


Fixed-1 | | Entities: 15 face(s) Type: Fixed Geometry

Resultant Forces

Components | X | Y | Z | Resultant
Reaction force(N) | -900.02 | 0.00491112 | -0.0124066 | 900.02
Reaction Moment(N.m) | 0 | 0 | 0 | 0

Load name | Load Image | Load Details


Force-1 | | Entities: 1 face(s) Type: Apply normal force Value: 900 N

# Connector Definitions

No Data

# Interaction Information

No Data

# Mesh information

Mesh type | Solid Mesh
Mesher Used: | Blended curvature-based mesh
Jacobian points for High quality mesh | 16 Points
Maximum element size | 6.41491 mm
Minimum element size | 2.13828 mm
Mesh Quality | High

## Mesh information - Details

Total Nodes | 21646
Total Elements | 12279
Maximum Aspect Ratio | 6.458
% of elements with Aspect Ratio < 3 | 99.5
Percentage of elements with Aspect Ratio > 10 | 0
Percentage of distorted elements | 0
Time to complete mesh(hh;mm;ss): | 00:00:02
Computer name: | ENGRLEANDZ

## Mesh Quality Plots

Name | Type | Min | Max
Quality1 | Mesh | - | -


Thigh Link-Static at 900N-Quality-Quality1

# Sensor Details

No Data

# Resultant Forces

## Reaction forces

Selection set | Units | Sum X | Sum Y | Sum Z | Resultant
Entire Model | N | -900.02 | 0.00491112 | -0.0124066 | 900.02

## Reaction Moments

Selection set | Units | Sum X | Sum Y | Sum Z | Resultant
Entire Model | N.m | 0 | 0 | 0 | 0

## Free body forces

Selection set | Units | Sum X | Sum Y | Sum Z | Resultant
Entire Model | N | -0.00141203 | 0.0655578 | -0.0363403 | 0.0749696

## Free body moments

Selection set | Units | Sum X | Sum Y | Sum Z | Resultant
Entire Model | N.m | 0 | 0 | 0 | 1e-33

# Beams

No Data

# Study Results

Name | Type | Min | Max
Stress1 | VON: von Mises Stress | 273.906N/m^2 Node: 18226 | 43,162,712.000N/m^2 Node: 20430


Thigh Link-Static at 900N-Stress-Stress1

Name | Type | Min | Max
Displacement1 | URES: Resultant Displacement | 0.000e+00mm Node: 1 | 1.446e-01mm Node: 20783


Thigh Link-Static at 900N-Displacement-Displacement1

Name | Type | Min | Max
Strain1 | ESTRN: Equivalent Strain | 3.969e-08 Element: 8823 | 3.936e-04 Element: 8144


Thigh Link-Static at 900N-Strain-Strain1

# Conclusion

Analyzed with SOLIDWORKS Simulation Simulation of Thigh Link 16

Analyzed with SOLIDWORKS Simulation Simulation of Thigh Link 1

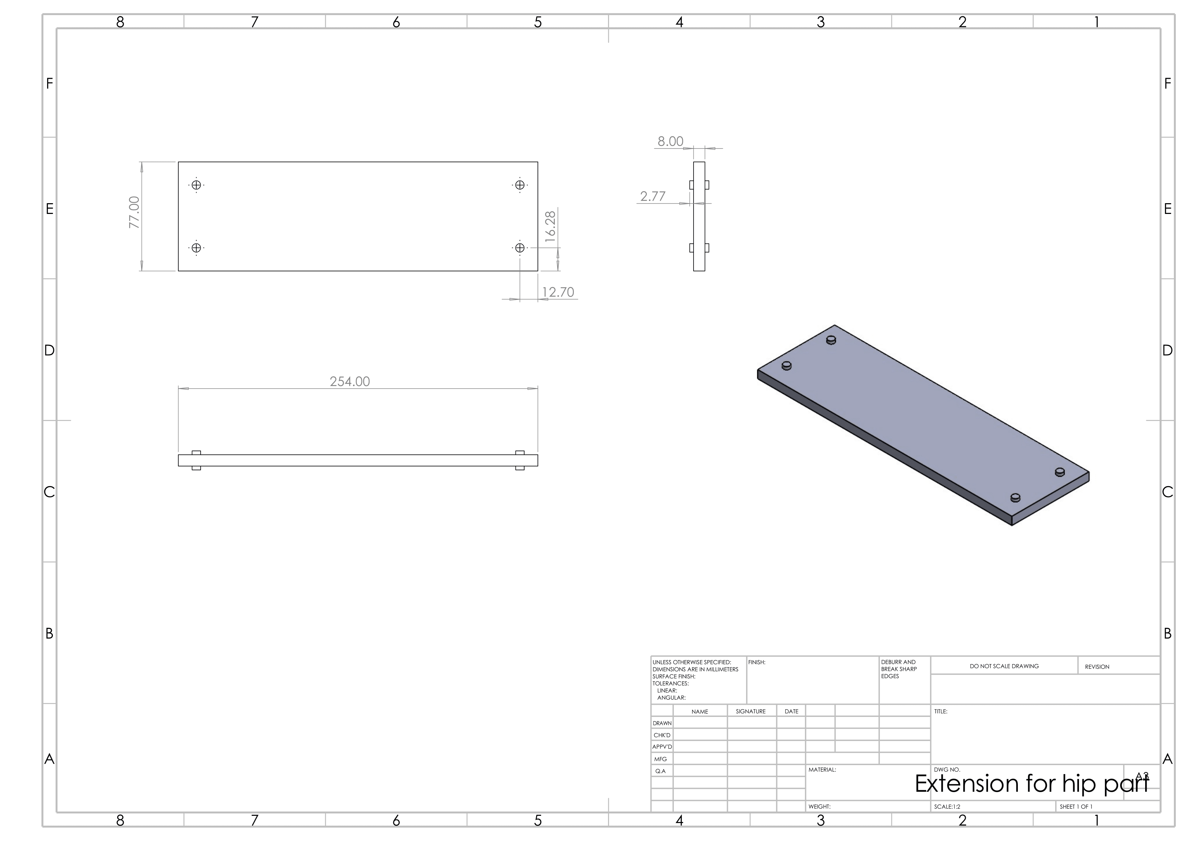
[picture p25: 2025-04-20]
3D Redesign/Exoskeleton-Recreated/3D from Adia et. al/pdf2png/Extension for hip part/Extension for hip part-1.png

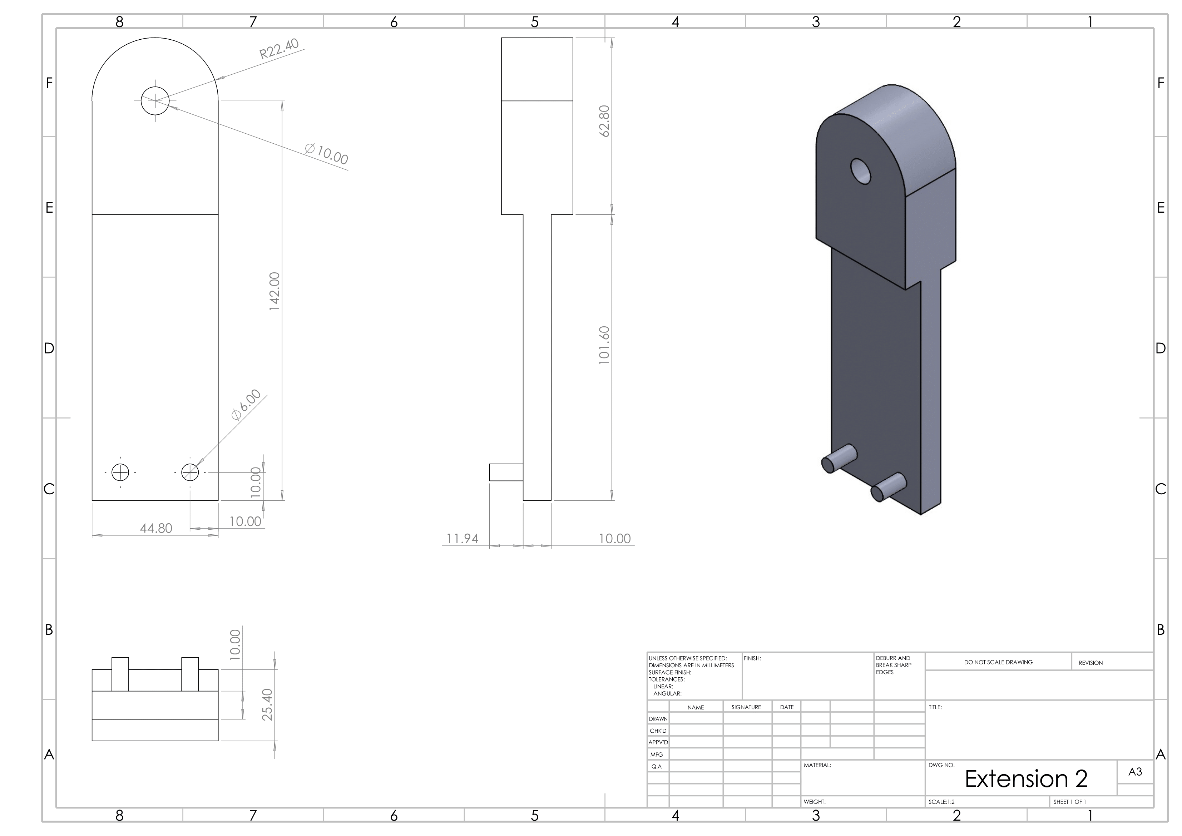
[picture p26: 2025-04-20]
3D Redesign/Exoskeleton-Recreated/3D from Adia et. al/pdf2png/Extension 2 Dimension/Extension 2 Dimension-1.png

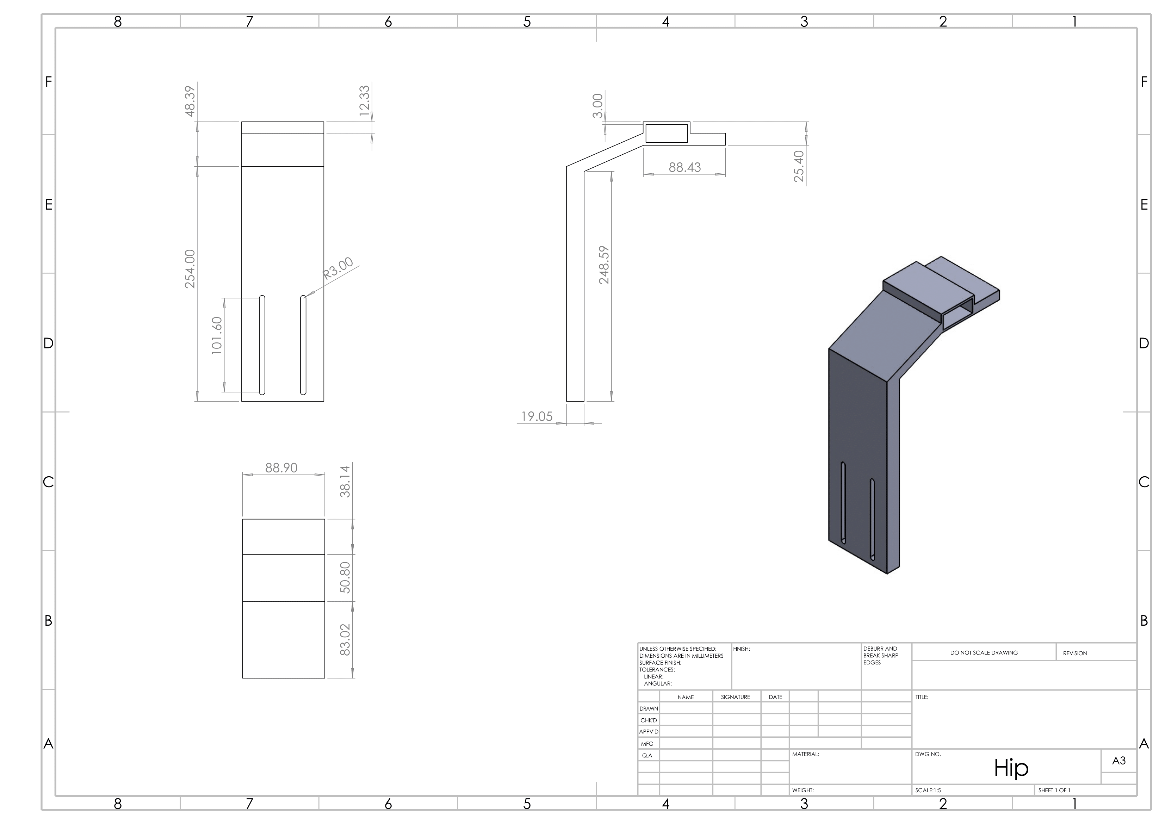
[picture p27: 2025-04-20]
3D Redesign/Exoskeleton-Recreated/3D from Adia et. al/pdf2png/Hip Dimension/Hip Dimension-1.png

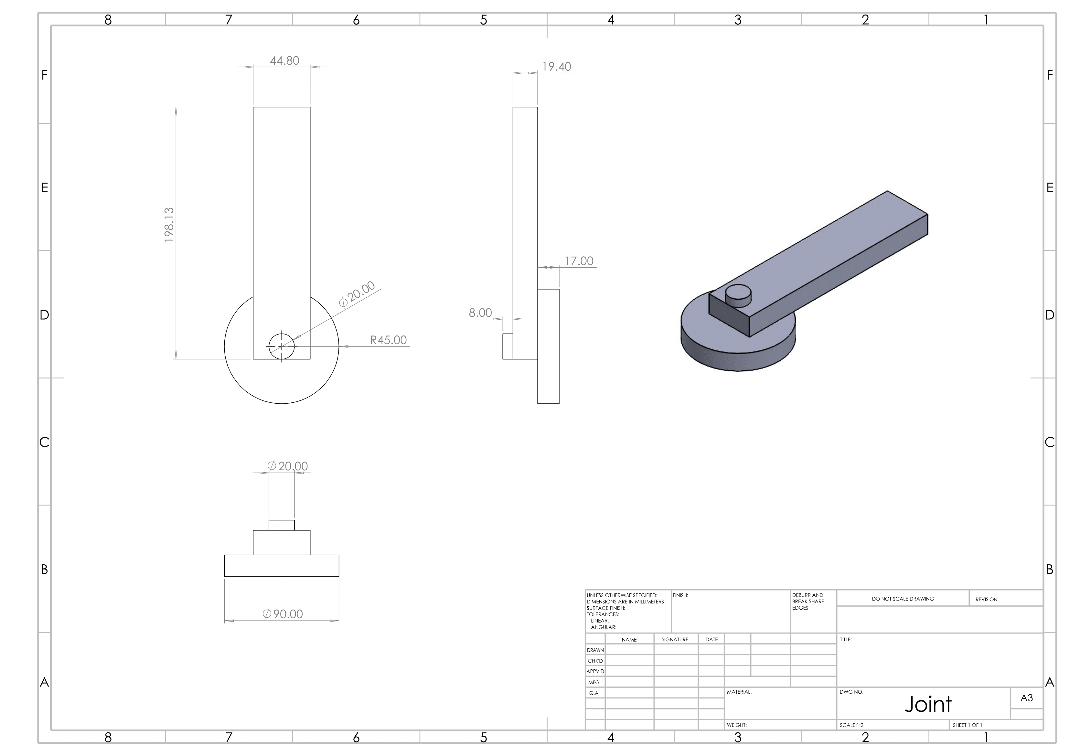
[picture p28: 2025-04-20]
3D Redesign/Exoskeleton-Recreated/3D from Adia et. al/pdf2png/Joint/Joint-1.png

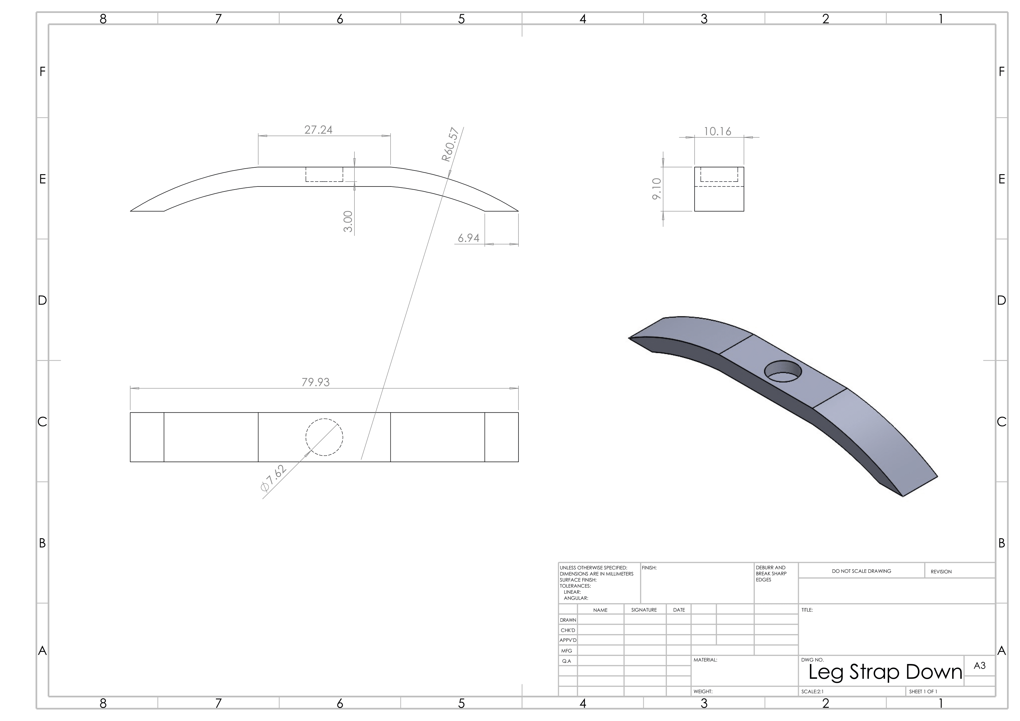
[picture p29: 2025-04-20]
3D Redesign/Exoskeleton-Recreated/3D from Adia et. al/pdf2png/Leg Strap Down/Leg Strap Down-1.png

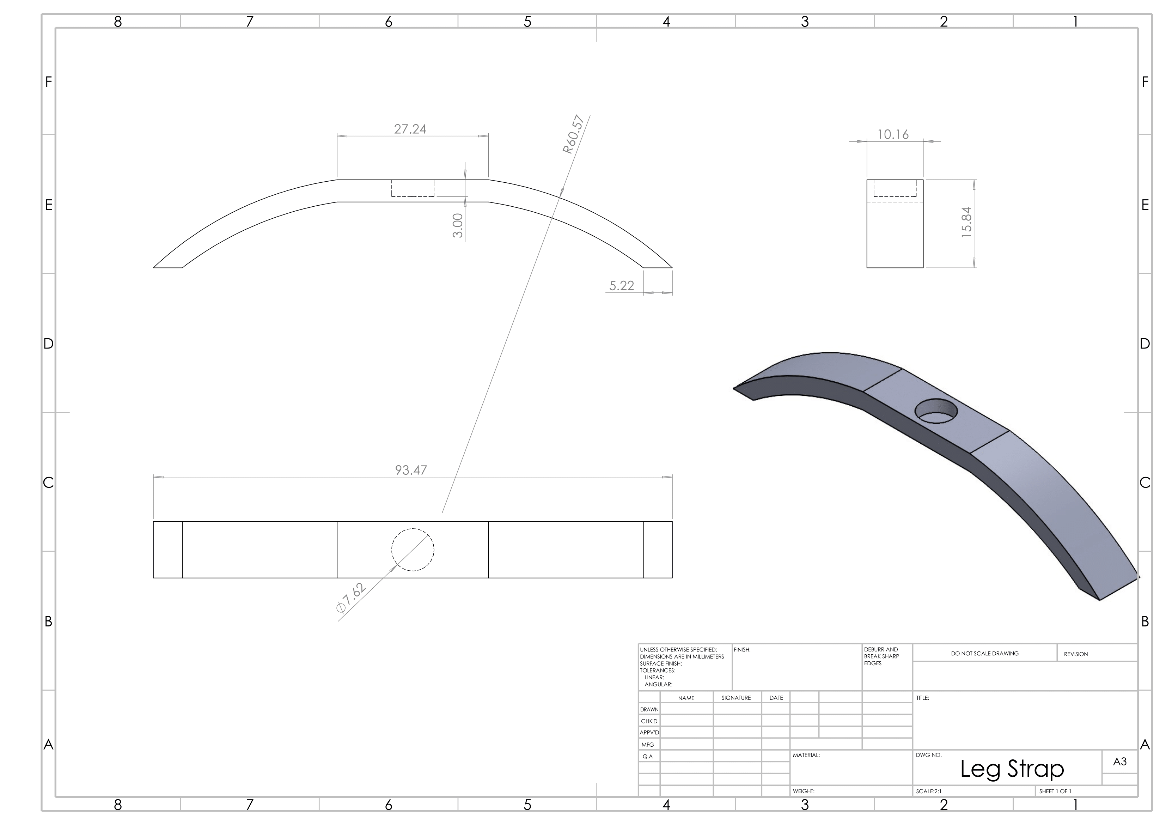
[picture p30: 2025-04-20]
3D Redesign/Exoskeleton-Recreated/3D from Adia et. al/pdf2png/Leg Strap/Leg Strap-1.png

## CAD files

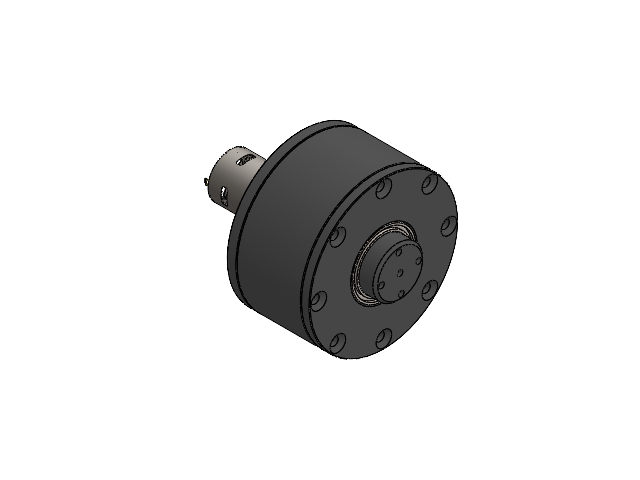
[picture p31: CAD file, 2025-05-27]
3D Redesign/Cyclodial Drive V4.0/Cyclodial gearbox v.4.0.SLDASM
RS550 12V DC Motor rev a
DC Shaft Coupllinggg
INNER COVER REVA
Dowel Pin for Assembly REVA x 13
DOWEL PIN HOUSING REVA
Eccentric Coupling Shaft rev b x 2
radial ball bearing_68_iso x 6
Shaft Spacing for Output x 2
Cyclodial Gear Stage 2 rev a x 2
Cyclodial Gear rev a x 3
Output Shaft Rev a
OUTPUT COVER REVA
socket head cap screw_iso x 2

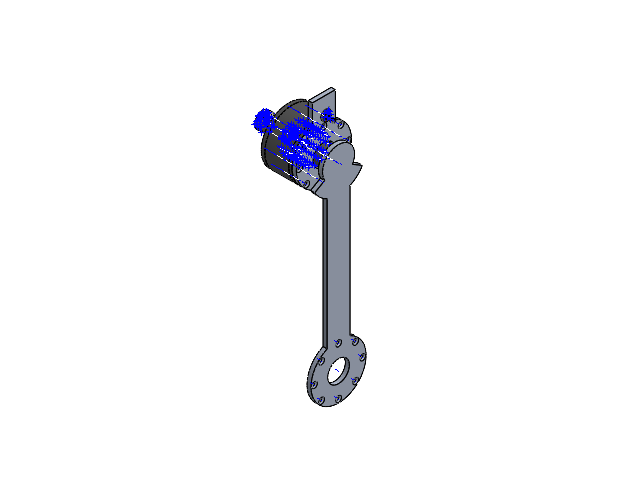
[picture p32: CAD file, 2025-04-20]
3D Redesign/Exoskeleton with Electronic Components/Idea 1.SLDASM
Hip Joint
Thigh Link
RS550 12V DC Motor
INNER COVER REVA
DC Shaft Coupler
Dowel Pin for Assembly REVA x 13
Bushing x 117
Eccentric Coupling Shaft x 2
radial ball bearing_68_iso x 5
Cyclodial Gear x 3
Shaft Spacing for Stage Two
Cyclodial Gear Stage Two
Shaft Spacing for Output
Output Shaft
DOWEL PIN HOUSING REVA
OUTPUT COVER REVA
countersunk slotted raised head screw_iso x 2
Potentiometer

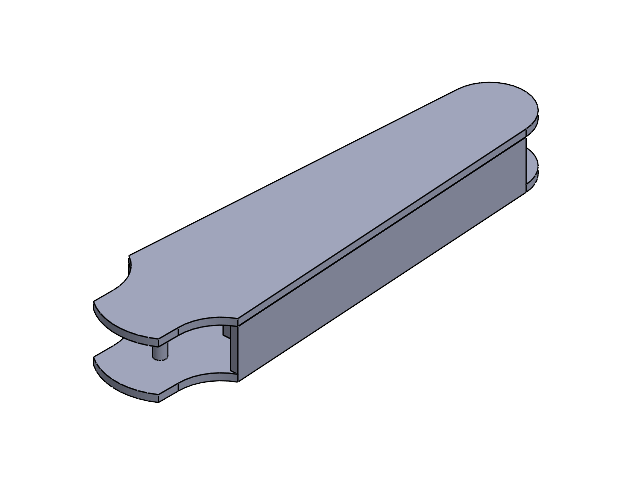
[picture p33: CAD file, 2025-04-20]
3D Redesign/Exoskeleton-Recreated/3D from Adia et. al/Leg/Leg Assembly.SLDASM
Leg
Leg Cover

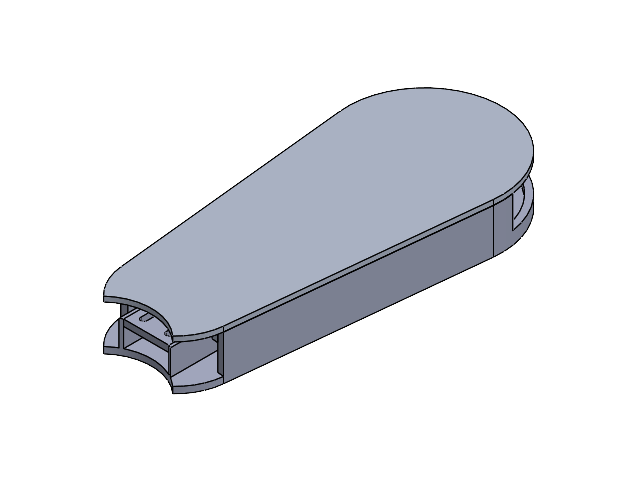
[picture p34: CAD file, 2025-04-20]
3D Redesign/Exoskeleton-Recreated/3D from Adia et. al/Thigh/Thigh Assembly.SLDASM
Thigh
Thigh Cover
Thigh Small Cover

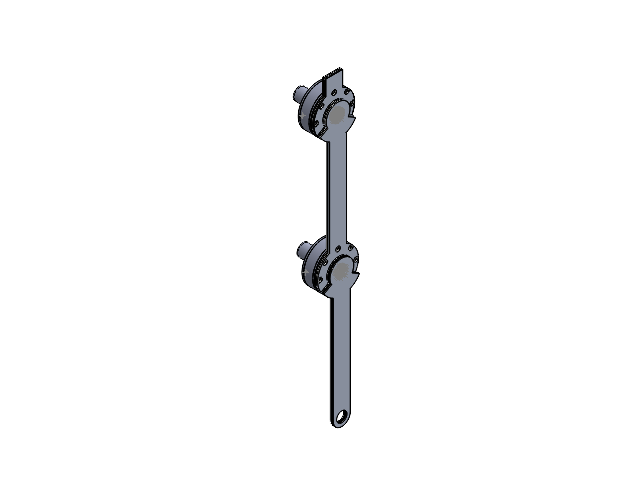
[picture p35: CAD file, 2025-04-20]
3D Redesign/Exoskeleton/Using ACP and Flatbar/Exoskeleton Assembly.SLDASM
Hip Joint 1st Layer
Hip Joint 2nd Layer
Hip Joint 3rd Layer
Thigh Link 1st Layer
Thigh Link 2nd Layer x 2
Leg Link 2nd and 3rd Layer x 2
Leg Link 1st Layer

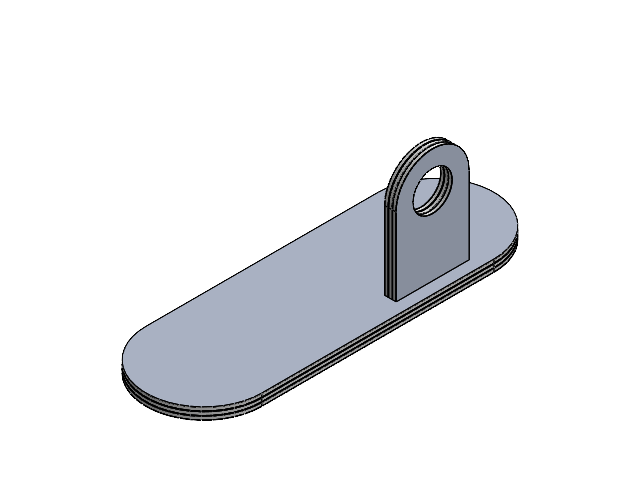
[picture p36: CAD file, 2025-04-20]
3D Redesign/Exoskeleton/Using ACP and Flatbar/Foot/Left/Foot Left Assembly.SLDASM
Foot layer 3L
Foot layer 1 and 2L x 2
Foot Joint x 3

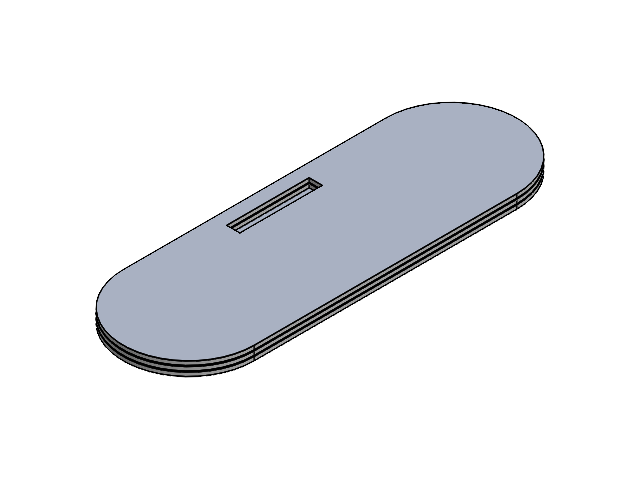
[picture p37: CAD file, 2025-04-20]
3D Redesign/Exoskeleton/Using ACP and Flatbar/Foot/Right/Foot flat assembly.SLDASM
Foot layer 3
Foot layer 1 and 2 x 2

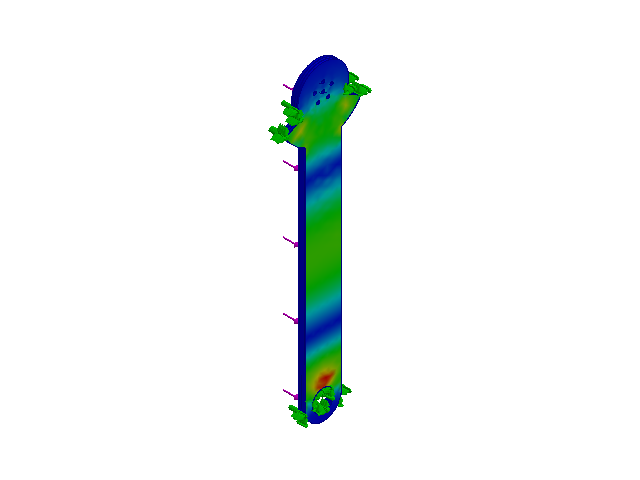
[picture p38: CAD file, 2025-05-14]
3D Redesign/Exoskeleton/Using ACP and Flatbar/Leg/Leg Assembly.SLDASM
Leg Link 2nd and 3rd Layer x 2
Leg Link 1st Layer

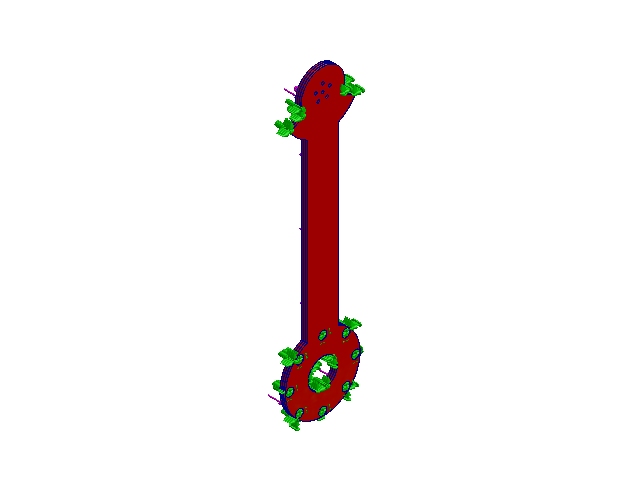
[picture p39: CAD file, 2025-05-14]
3D Redesign/Exoskeleton/Using ACP and Flatbar/Thigh/Thigh Assembly.SLDASM
Thigh Link 1st Layer
Thigh Link 2nd Layer x 2

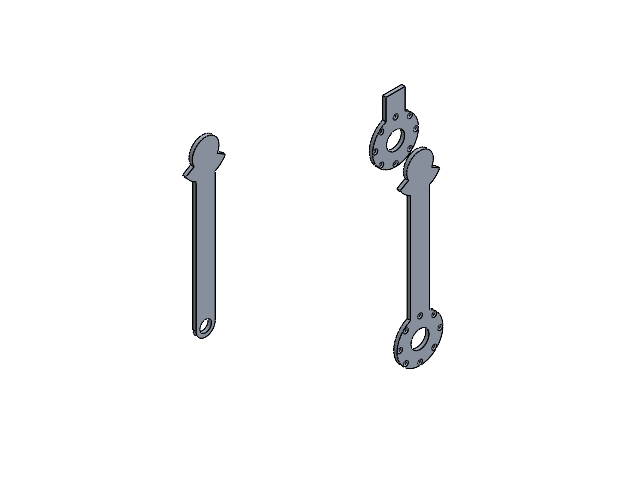
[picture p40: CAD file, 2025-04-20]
3D Redesign/Exoskeleton/Using Aluminum 6061/Final Exoskeleton/Final Exoskeleton Assembly.SLDASM
Hip Joint
Thigh Link
Leg Link

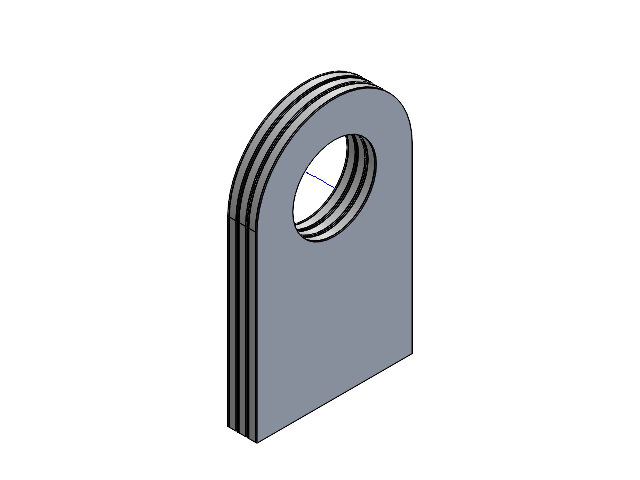
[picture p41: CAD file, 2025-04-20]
3D Redesign/Exoskeleton/Using ACP and Flatbar/Foot/Left/Foot Joint Assembly.SLDASM
Foot Joint x 3

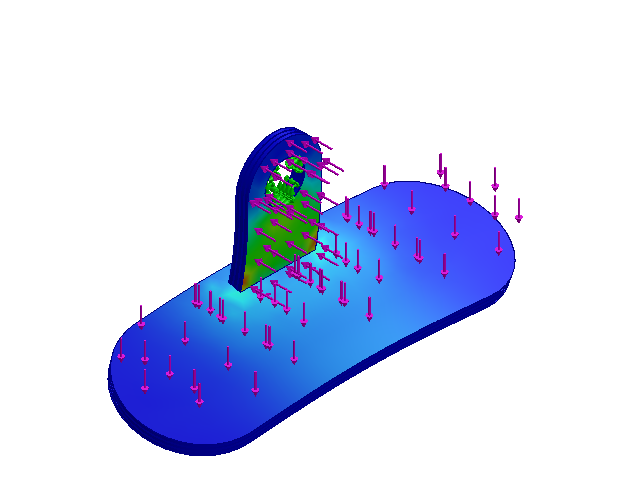
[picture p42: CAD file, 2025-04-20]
3D Redesign/Exoskeleton/Using ACP and Flatbar/Foot/Right/Foot Assembly R.SLDASM
Foot layer 3
Foot layer 1 and 2 x 2
Foot Joint x 3

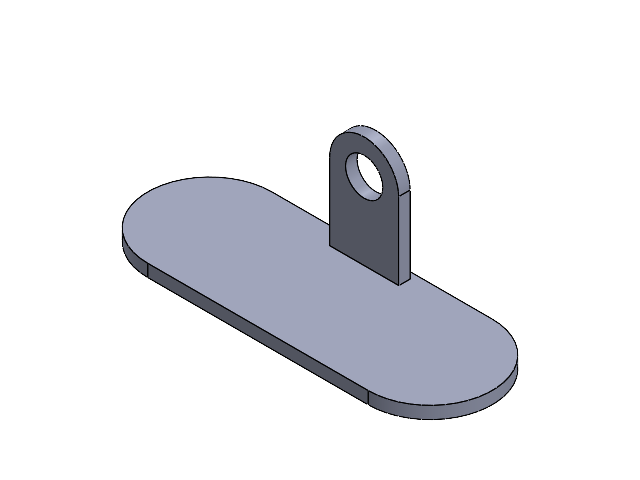
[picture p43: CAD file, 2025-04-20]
3D Redesign/Exoskeleton/Using Aluminum 6061/Foot/Foot.SLDASM
Foot-001
Foot-002

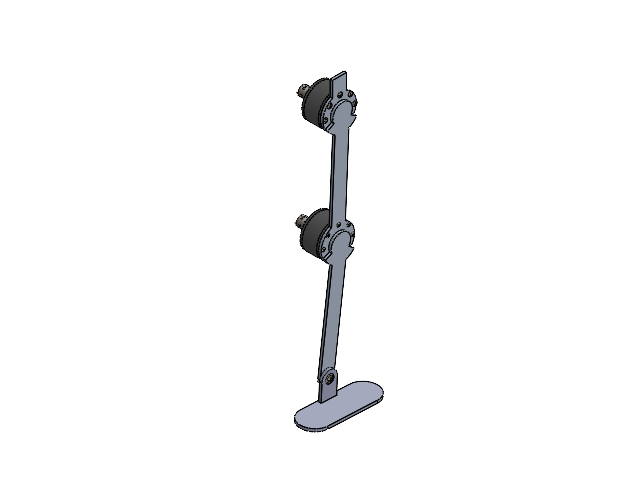
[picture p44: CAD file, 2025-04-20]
3D Redesign/Exoskeleton/Using Aluminum 6061/Exoskeleton Assembly Aluminum.SLDASM
Hip Joint
Thigh Link
Leg Link
Foot-001
Foot-002
RS550 12V DC Motor x 2
INNER COVER REVA x 2
DC Shaft Coupler x 2
Dowel Pin for Assembly REVA x 26
Bushing x 234
Eccentric Coupling Shaft x 4
radial ball bearing_68_iso x 12
Cyclodial Gear x 6
Shaft Spacing for Stage Two x 2
Cyclodial Gear Stage Two x 2
Shaft Spacing for Output x 2
Output Shaft x 2
DOWEL PIN HOUSING REVA x 2
OUTPUT COVER REVA x 2
countersunk slotted raised head screw_iso x 4
hexa csunk flathd screw_iso x 16

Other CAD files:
3D Redesign/Exoskeleton/Using ACP and Flatbar/Foot/Left/Foot Joint Sub asm.SLDASM
3D Redesign/Cyclodial Drive V3.0/12 tooth for coupling.SLDPRT
3D Redesign/Cyclodial Drive V3.0/Cyclodial Gear.SLDPRT
3D Redesign/Cyclodial Drive V3.0/DC Shaft Coupler.SLDPRT
3D Redesign/Cyclodial Drive V3.0/DOWEL PIN HOUSING REVA.SLDPRT
3D Redesign/Cyclodial Drive V3.0/Definition of Roller REVA.SLDPRT
3D Redesign/Cyclodial Drive V3.0/Distance Ring.SLDPRT
3D Redesign/Cyclodial Drive V3.0/Eccentric Coupling Shaft Second Stage.SLDPRT
3D Redesign/Cyclodial Drive V3.0/Eccentric Coupling Shaft.SLDPRT
3D Redesign/Cyclodial Drive V3.0/Gearbox.SLDASM
3D Redesign/Cyclodial Drive V3.0/INNER COVER REVA.SLDPRT
3D Redesign/Cyclodial Drive V3.0/OUTPUT COVER REVA.SLDPRT
3D Redesign/Cyclodial Drive V3.0/Part1.SLDPRT
3D Redesign/Cyclodial Drive V3.0/RS550 12V DC Motor.SLDPRT
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

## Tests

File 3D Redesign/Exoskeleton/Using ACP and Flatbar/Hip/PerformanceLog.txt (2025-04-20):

Number of Contacts: 24
Number of contact data: 9790

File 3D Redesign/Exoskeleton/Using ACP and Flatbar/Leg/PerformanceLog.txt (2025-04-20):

Number of Contacts: 8
Number of contact data: 4717

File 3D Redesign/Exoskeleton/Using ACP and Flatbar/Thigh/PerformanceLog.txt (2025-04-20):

Number of Contacts: 24
Number of contact data: 10565

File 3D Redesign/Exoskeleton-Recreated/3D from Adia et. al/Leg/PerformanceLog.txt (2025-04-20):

Number of Contacts: 5
Number of contact data: 1868

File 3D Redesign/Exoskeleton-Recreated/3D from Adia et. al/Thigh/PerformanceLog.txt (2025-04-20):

Number of Contacts: 5
Number of contact data: 1777

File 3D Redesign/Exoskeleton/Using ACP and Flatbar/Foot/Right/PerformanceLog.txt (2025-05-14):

Number of Contacts: 145
Number of contact data: 6329

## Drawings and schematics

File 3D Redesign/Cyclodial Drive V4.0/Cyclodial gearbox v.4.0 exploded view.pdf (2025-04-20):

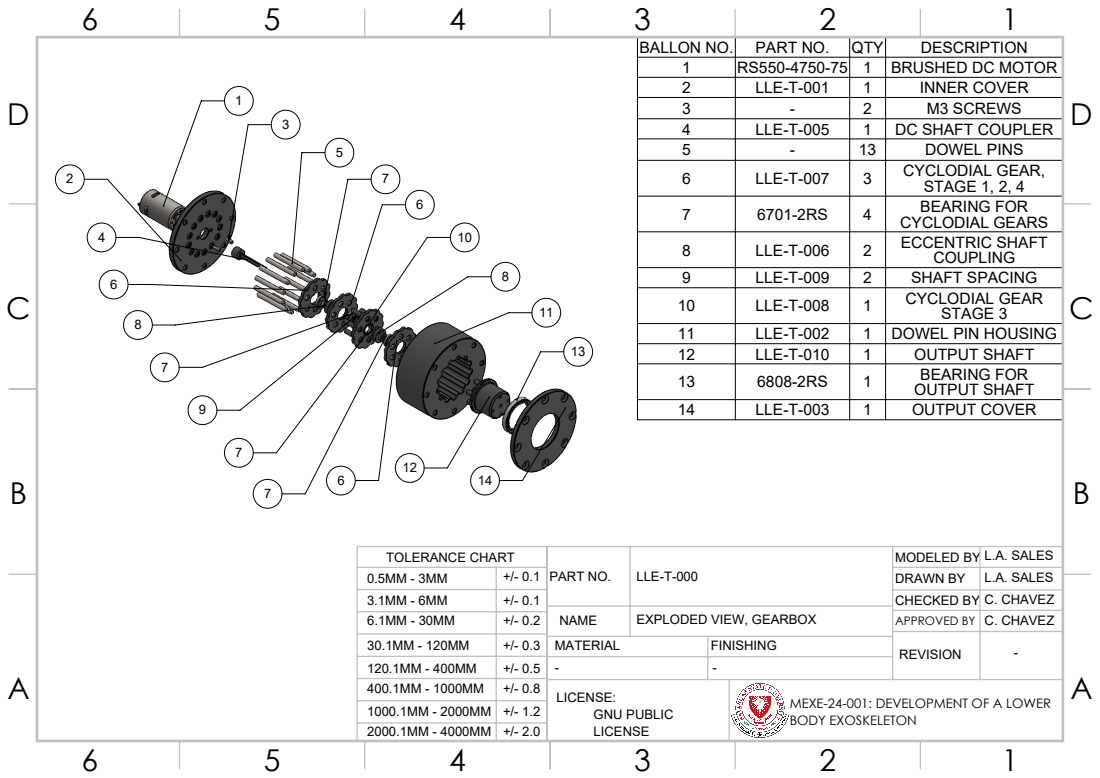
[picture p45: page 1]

BALLON NO. | PART NO. | QTY | DESCRIPTION
1 | RS550-4750-75 | 1 | BRUSHED DC MOTOR
2 | LLE-T-001 | 1 | INNER COVER
3 | - | 2 | M3 SCREWS
4 | LLE-T-005 | 1 | DC SHAFT COUPLER
5 | - | 13 | DOWEL PINS
6 | LLE-T-007 | 3 | CYCLODIAL GEAR, STAGE 1, 2, 4
7 | 6701-2RS | 4 | BEARING FOR CYCLODIAL GEARS
8 | LLE-T-006 | 2 | ECCENTRIC SHAFT COUPLING
9 | LLE-T-009 | 2 | SHAFT SPACING
10 | LLE-T-008 | 1 | CYCLODIAL GEAR STAGE 3
11 | LLE-T-002 | 1 | DOWEL PIN HOUSING
12 | LLE-T-010 | 1 | OUTPUT SHAFT
13 | 6808-2RS | 1 | BEARING FOR OUTPUT SHAFT
14 | LLE-T-003 | 1 | OUTPUT COVER

TOLERANCE CHART | PART NO. | LLE-T-000 | MODELED BY | L.A. SALES
0.5MM - 3MM | +/- 0.1 | | | DRAWN BY | L.A. SALES
3.1MM - 6MM | +/- 0.1 | | | CHECKED BY | C. CHAVEZ
6.1MM - 30MM | +/- 0.2 | | | APPROVED BY | C. CHAVEZ
30.1MM - 120MM | +/- 0.3 | MATERIAL | FINISHING | REVISION | -
120.1MM - 400MM | +/- 0.5 | - -
400.1MM - 1000MM | +/- 0.8 | LICENSE: GNU PUBLIC LICENSE | MEXE-24-001: DEVELOPMENT OF A LOWER BODY EXOSKELETON
1000.1MM - 2000MM | +/- 1.2
2000.1MM - 4000MM | +/- 2.0

NAME | EXPLODED VIEW, GEARBOX

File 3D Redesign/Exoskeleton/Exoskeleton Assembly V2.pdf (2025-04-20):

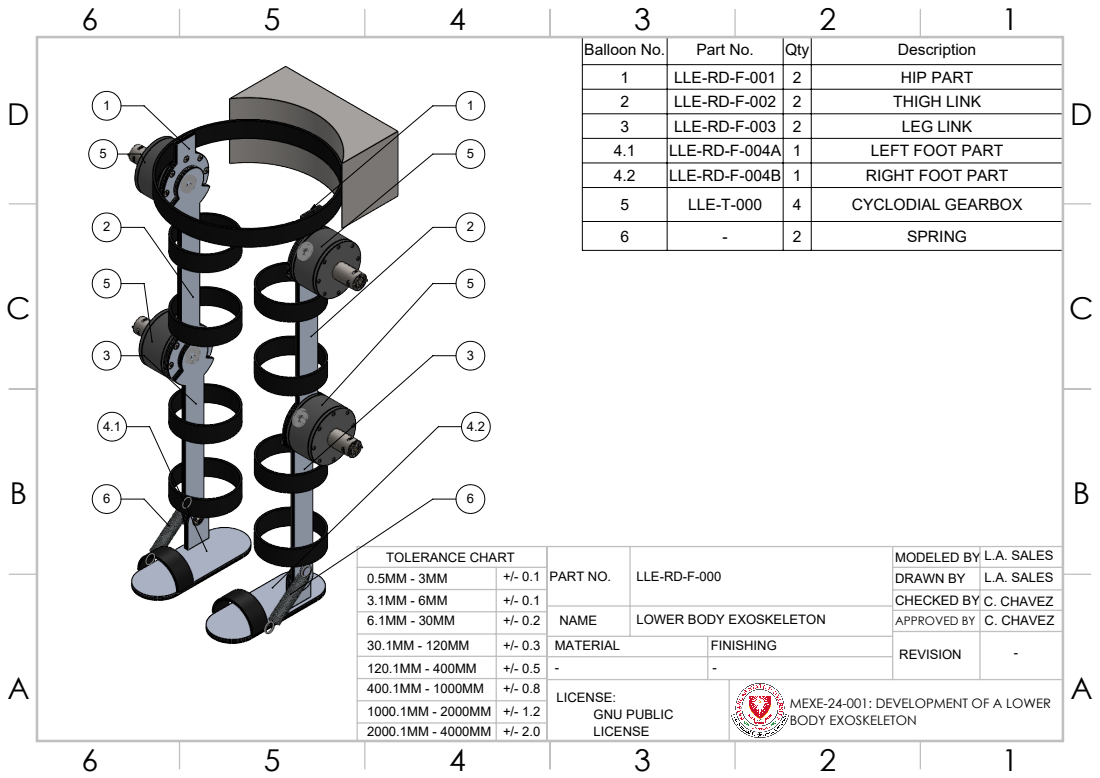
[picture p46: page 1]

Balloon No. | Part No. | Qty | Description
1 | LLE-RD-F-001 | 2 | HIP PART
2 | LLE-RD-F-002 | 2 | THIGH LINK
3 | LLE-RD-F-003 | 2 | LEG LINK
4.1 | LLE-RD-F-004A | 1 | LEFT FOOT PART
4.2 | LLE-RD-F-004B | 1 | RIGHT FOOT PART
5 | LLE-T-000 | 4 | CYCLODIAL GEARBOX
6 | - | 2 | SPRING

TOLERANCE CHART | PART NO. | LLE-RD-F-000 | MODELED BY | L.A. SALES
0.5MM - 3MM | +/- 0.1 | | | DRAWN BY | L.A. SALES
3.1MM - 6MM | +/- 0.1 | | | CHECKED BY | C. CHAVEZ
6.1MM - 30MM | +/- 0.2 | | | APPROVED BY | C. CHAVEZ
30.1MM - 120MM | +/- 0.3 | MATERIAL | FINISHING | REVISION | -
120.1MM - 400MM | +/- 0.5 | - -
400.1MM - 1000MM | +/- 0.8 | LICENSE: GNU PUBLIC LICENSE | MEXE-24-001: DEVELOPMENT OF A LOWER BODY EXOSKELETON
1000.1MM - 2000MM | +/- 1.2
2000.1MM - 4000MM | +/- 2.0

NAME | LOWER BODY EXOSKELETON

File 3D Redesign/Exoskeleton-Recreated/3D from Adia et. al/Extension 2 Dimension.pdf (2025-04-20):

E E

F F

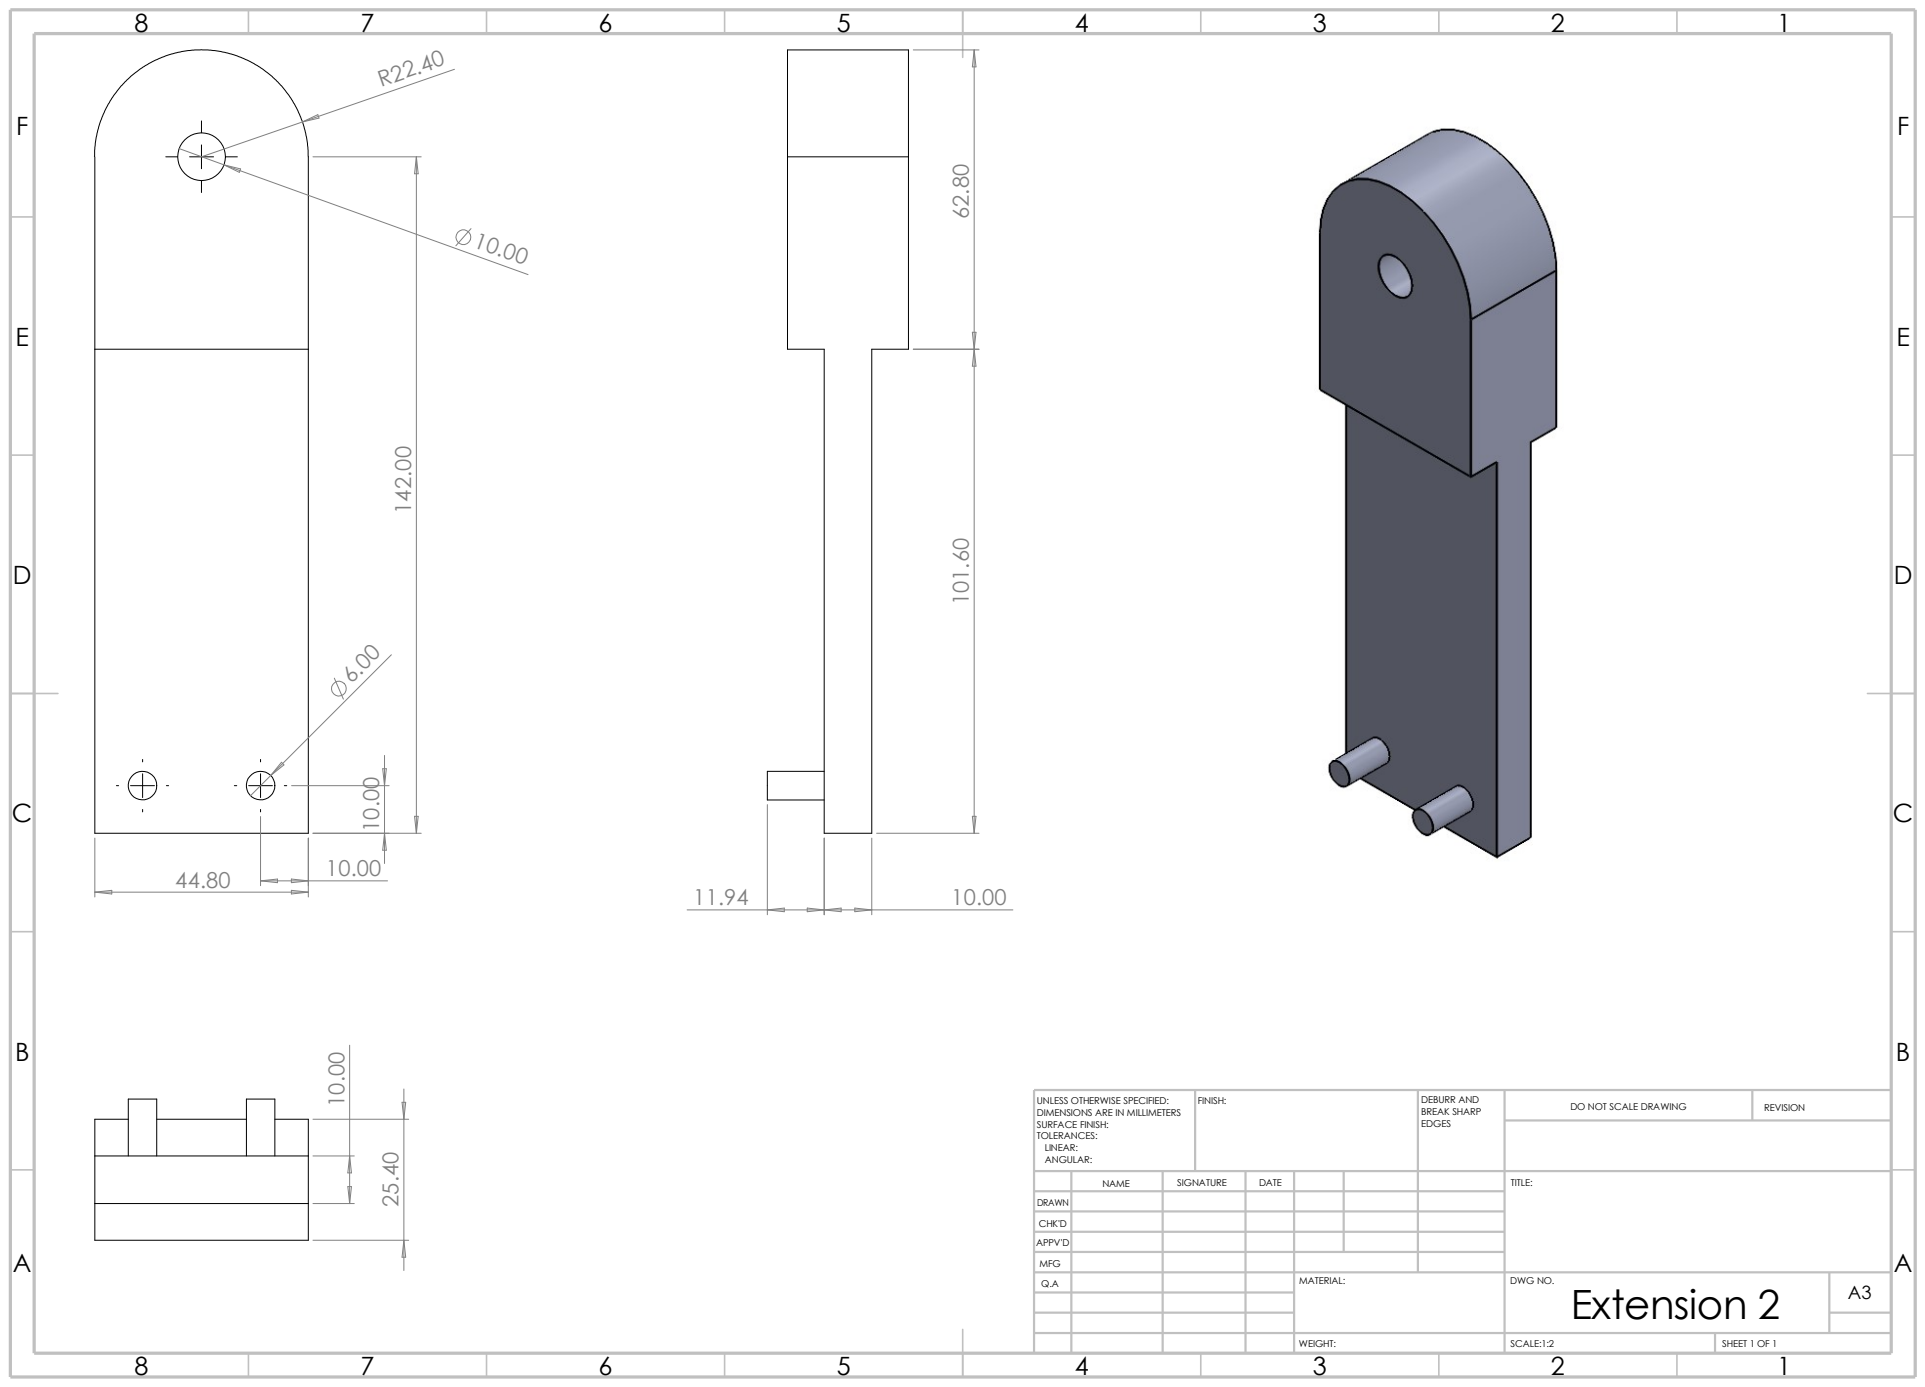
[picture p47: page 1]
SCALE:1:2; SHEET 1 OF 1; WEIGHT:; DO NOT SCALE DRAWING; REVISION; FINISH:; EDGES; DEBURR AND BREAK SHARP; Extension 2 ¹⁰¹.60 62.80

UNLESS OTHERWISE SPECIFIED:
DIMENSIONS ARE IN MILLIMETERS
SURFACE FINISH:
TOLERANCES:
LINEAR:
ANGULAR:

NAME | SIGNATURE | DATE | | | | TITLE:

DRAWN
CHK'D
APPV'D
Q.A | | | | MATERIAL: | DWG NO. | A3

MFG

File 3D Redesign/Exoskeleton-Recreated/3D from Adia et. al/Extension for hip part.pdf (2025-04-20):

E E

F F

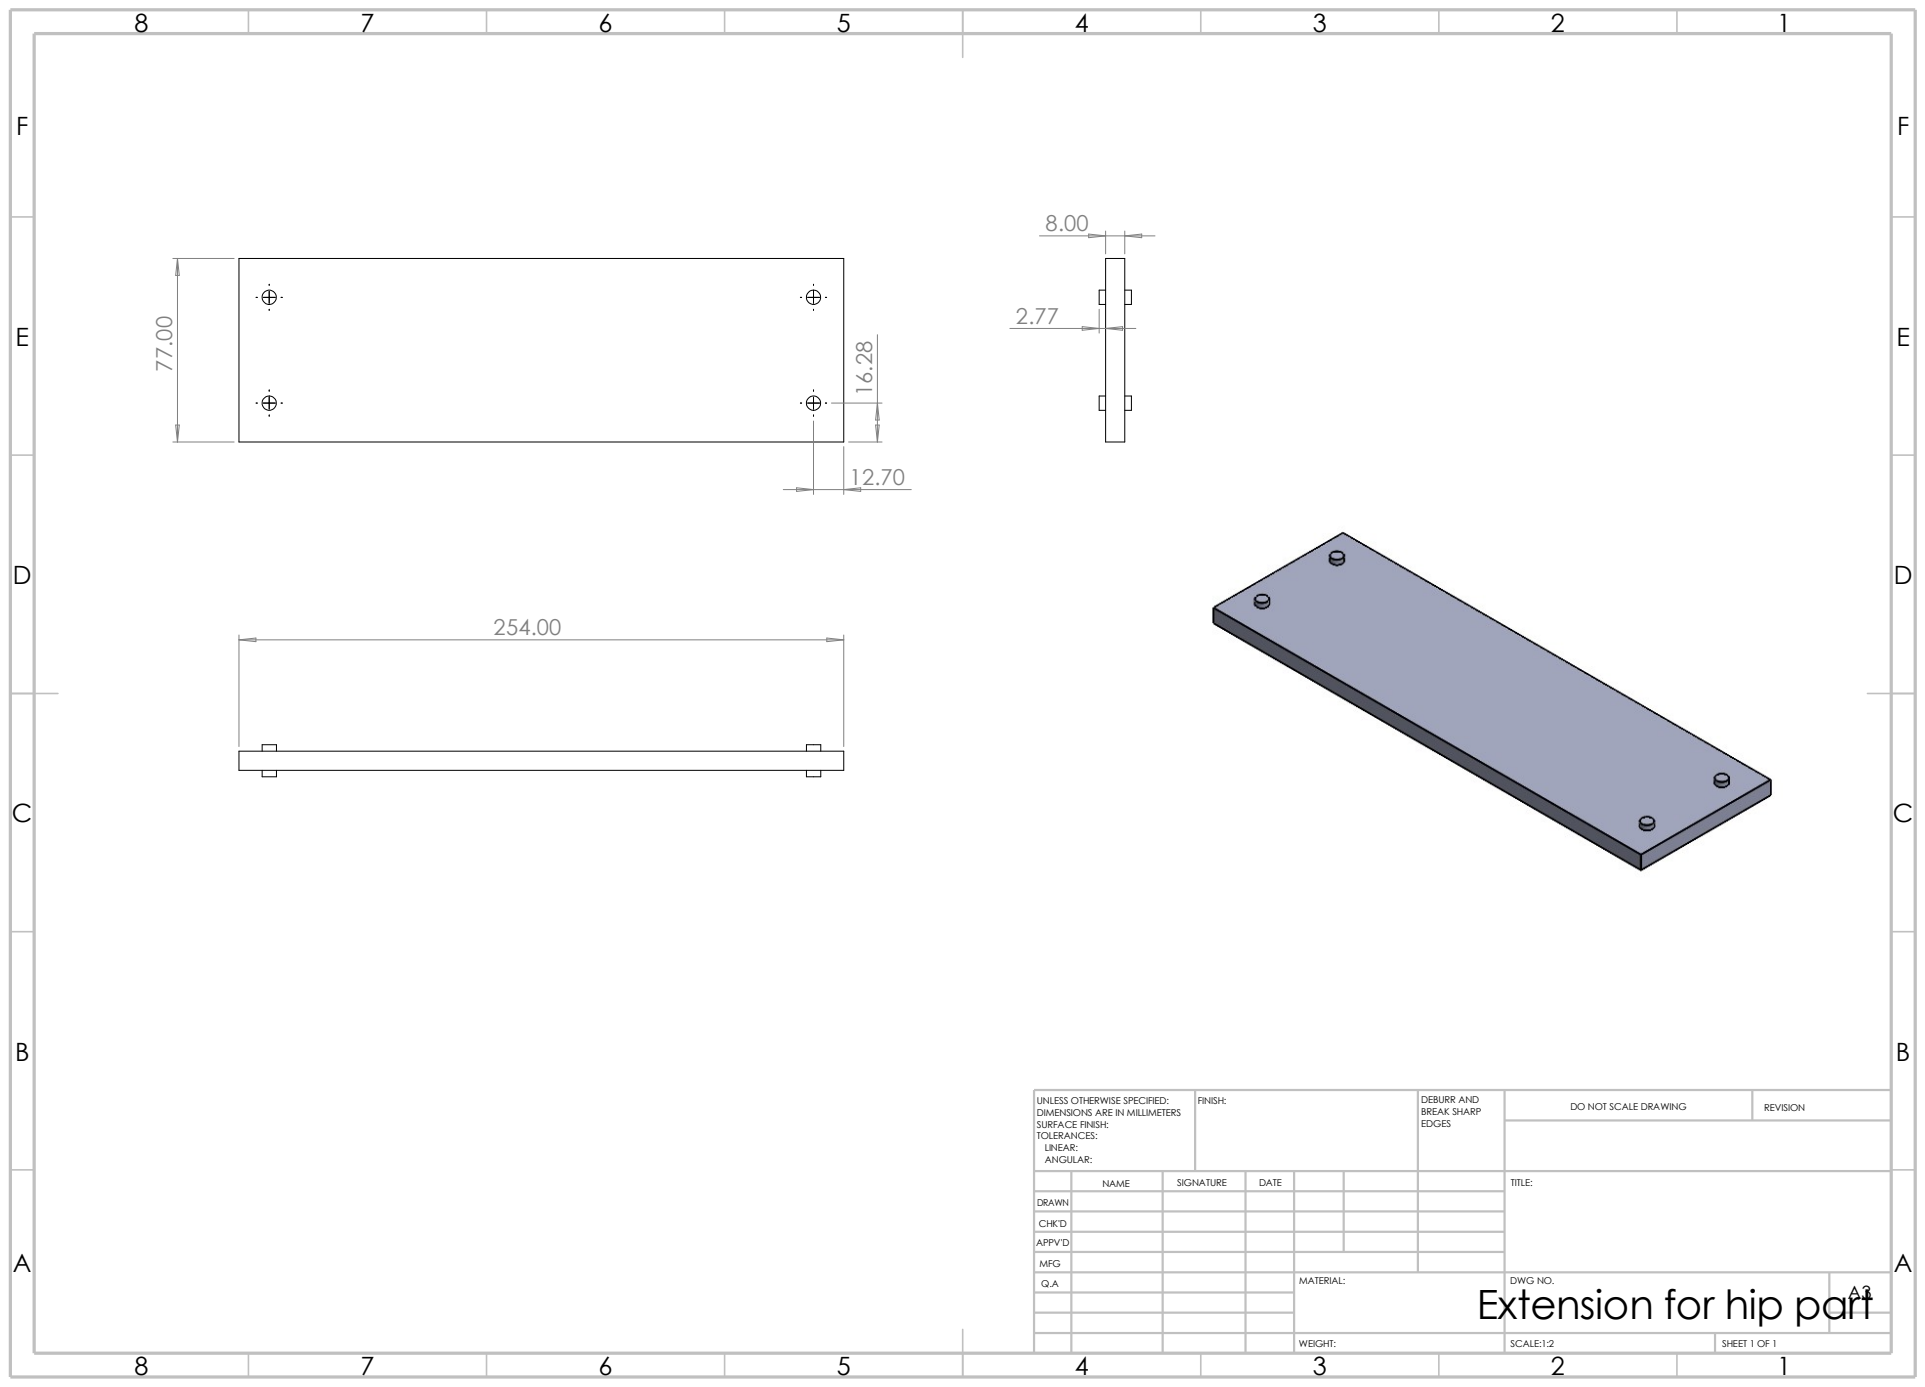
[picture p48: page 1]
SCALE:1:2; SHEET 1 OF 1; WEIGHT:; REVISION; FINISH:; EDGES; DEBURR AND BREAK SHARP

Extension for hip part ⁷⁷.00

UNLESS OTHERWISE SPECIFIED:
DIMENSIONS ARE IN MILLIMETERS
SURFACE FINISH:
TOLERANCES:
LINEAR:
ANGULAR:

DO NOT SCALE DRAWING

NAME | SIGNATURE | DATE | | | | TITLE:

DRAWN
CHK'D
APPV'D
Q.A | | | | MATERIAL: | DWG NO. | A3

MFG

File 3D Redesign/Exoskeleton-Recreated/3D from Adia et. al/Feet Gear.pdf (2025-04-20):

E E

F F

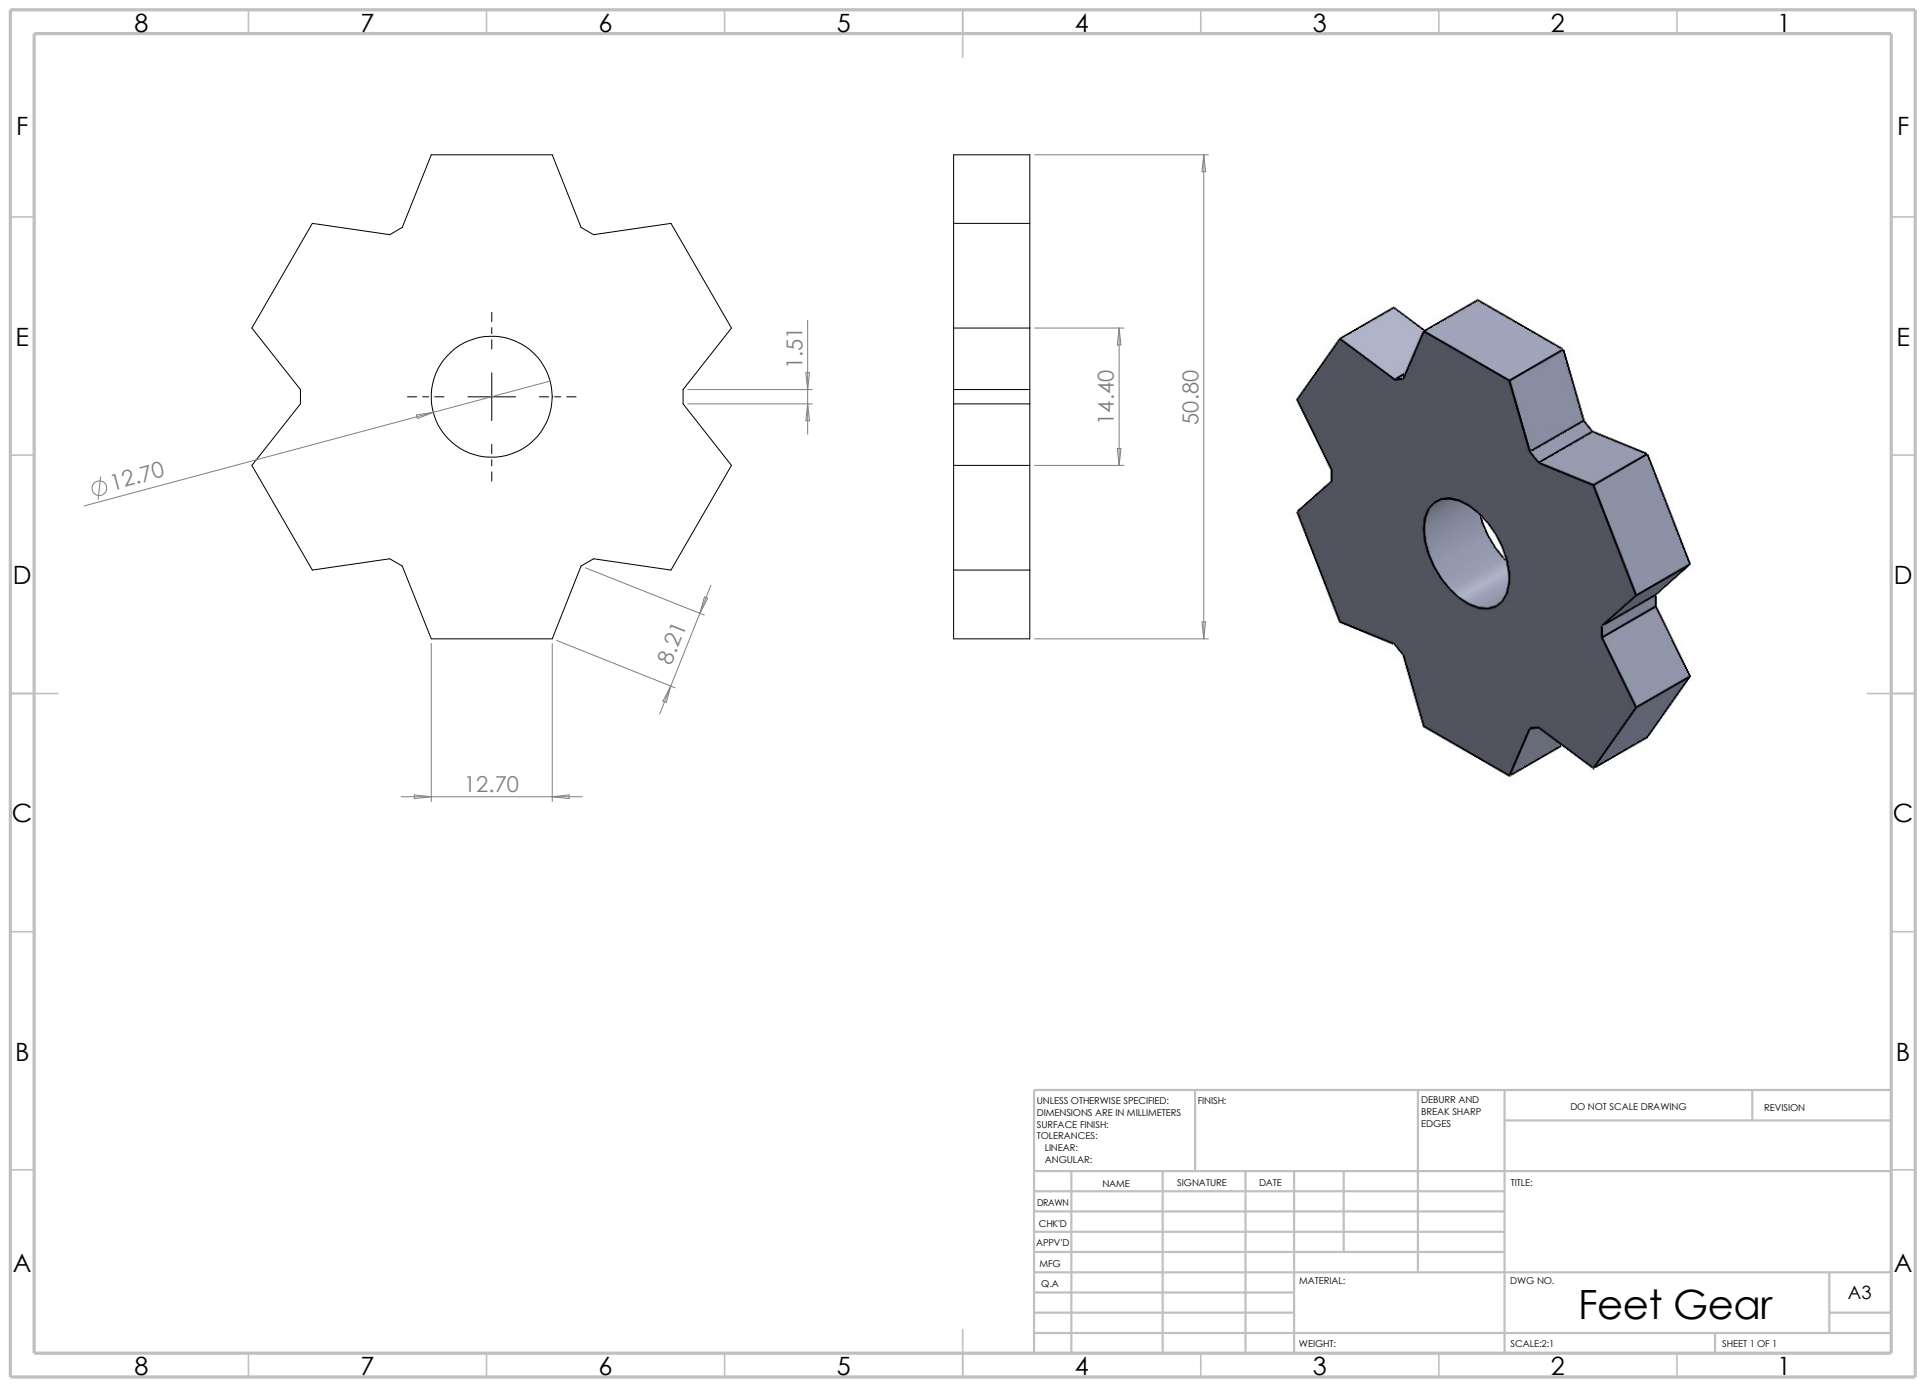
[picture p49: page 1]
SCALE:2:1; SHEET 1 OF 1; WEIGHT:; DO NOT SCALE DRAWING; REVISION; FINISH:; EDGES; DEBURR AND BREAK SHARP; Feet Gear ¹⁴.40

UNLESS OTHERWISE SPECIFIED:
DIMENSIONS ARE IN MILLIMETERS
SURFACE FINISH:
TOLERANCES:
LINEAR:
ANGULAR:

NAME | SIGNATURE | DATE | | | | TITLE:

DRAWN
CHK'D
APPV'D

MFG
Q.A | | | | MATERIAL: | DWG NO. | A3

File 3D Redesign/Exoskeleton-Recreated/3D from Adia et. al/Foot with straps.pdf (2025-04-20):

E E

F F

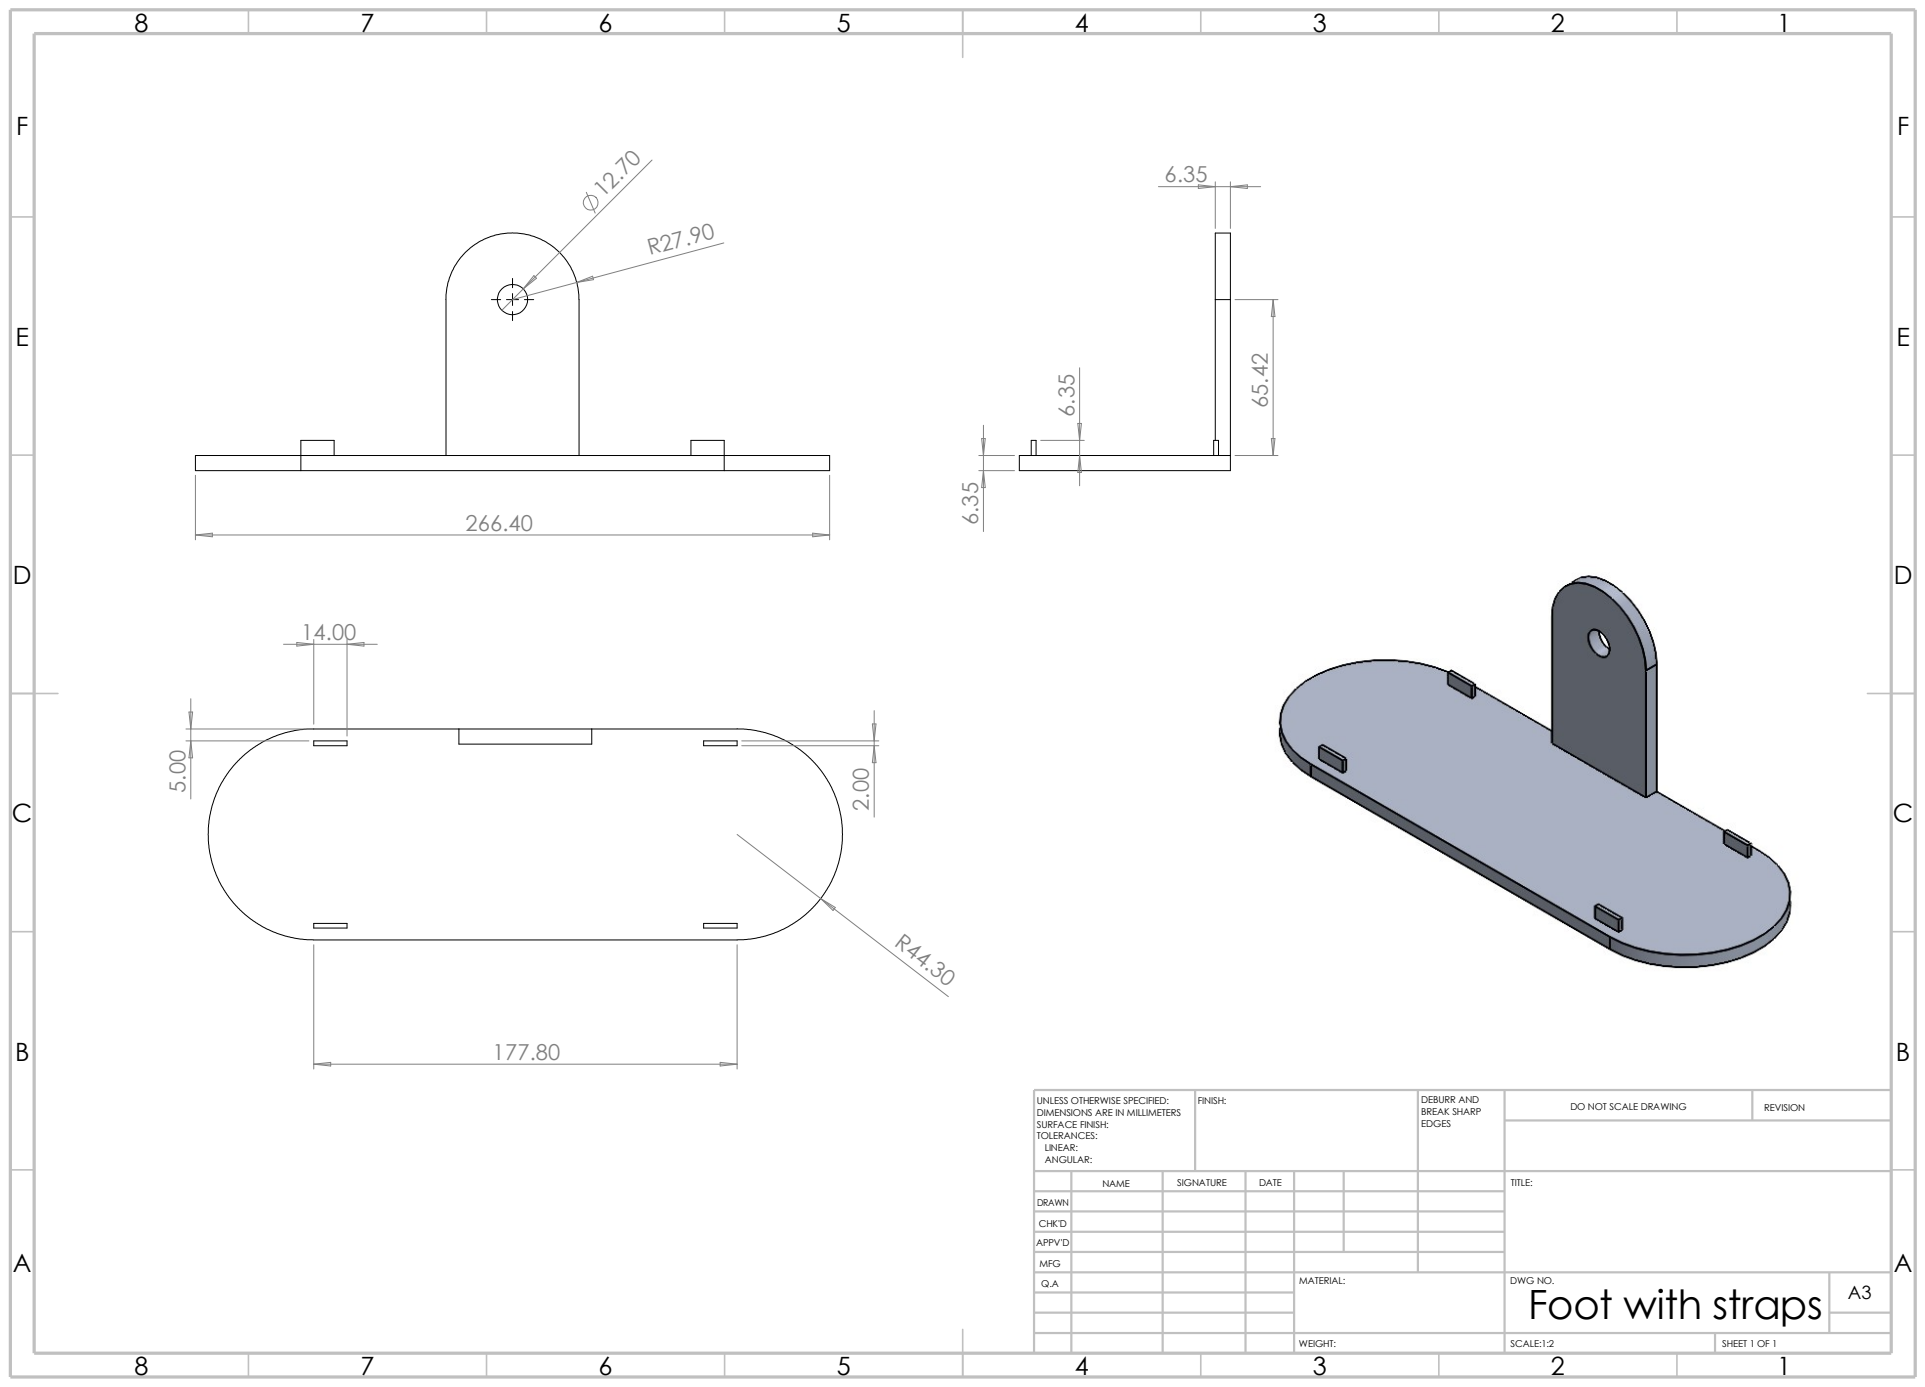
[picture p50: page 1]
SCALE:1:2; SHEET 1 OF 1; WEIGHT:; REVISION; FINISH:; EDGES; DEBURR AND BREAK SHARP

UNLESS OTHERWISE SPECIFIED:
DIMENSIONS ARE IN MILLIMETERS
SURFACE FINISH:
TOLERANCES:
LINEAR:
ANGULAR:

DO NOT SCALE DRAWING

NAME | SIGNATURE | DATE | | | | TITLE:

DRAWN
CHK'D
APPV'D
Q.A | | | | MATERIAL: | DWG NO. Foot with straps | A3

MFG

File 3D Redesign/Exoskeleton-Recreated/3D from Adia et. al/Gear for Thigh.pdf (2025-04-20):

E E

F F

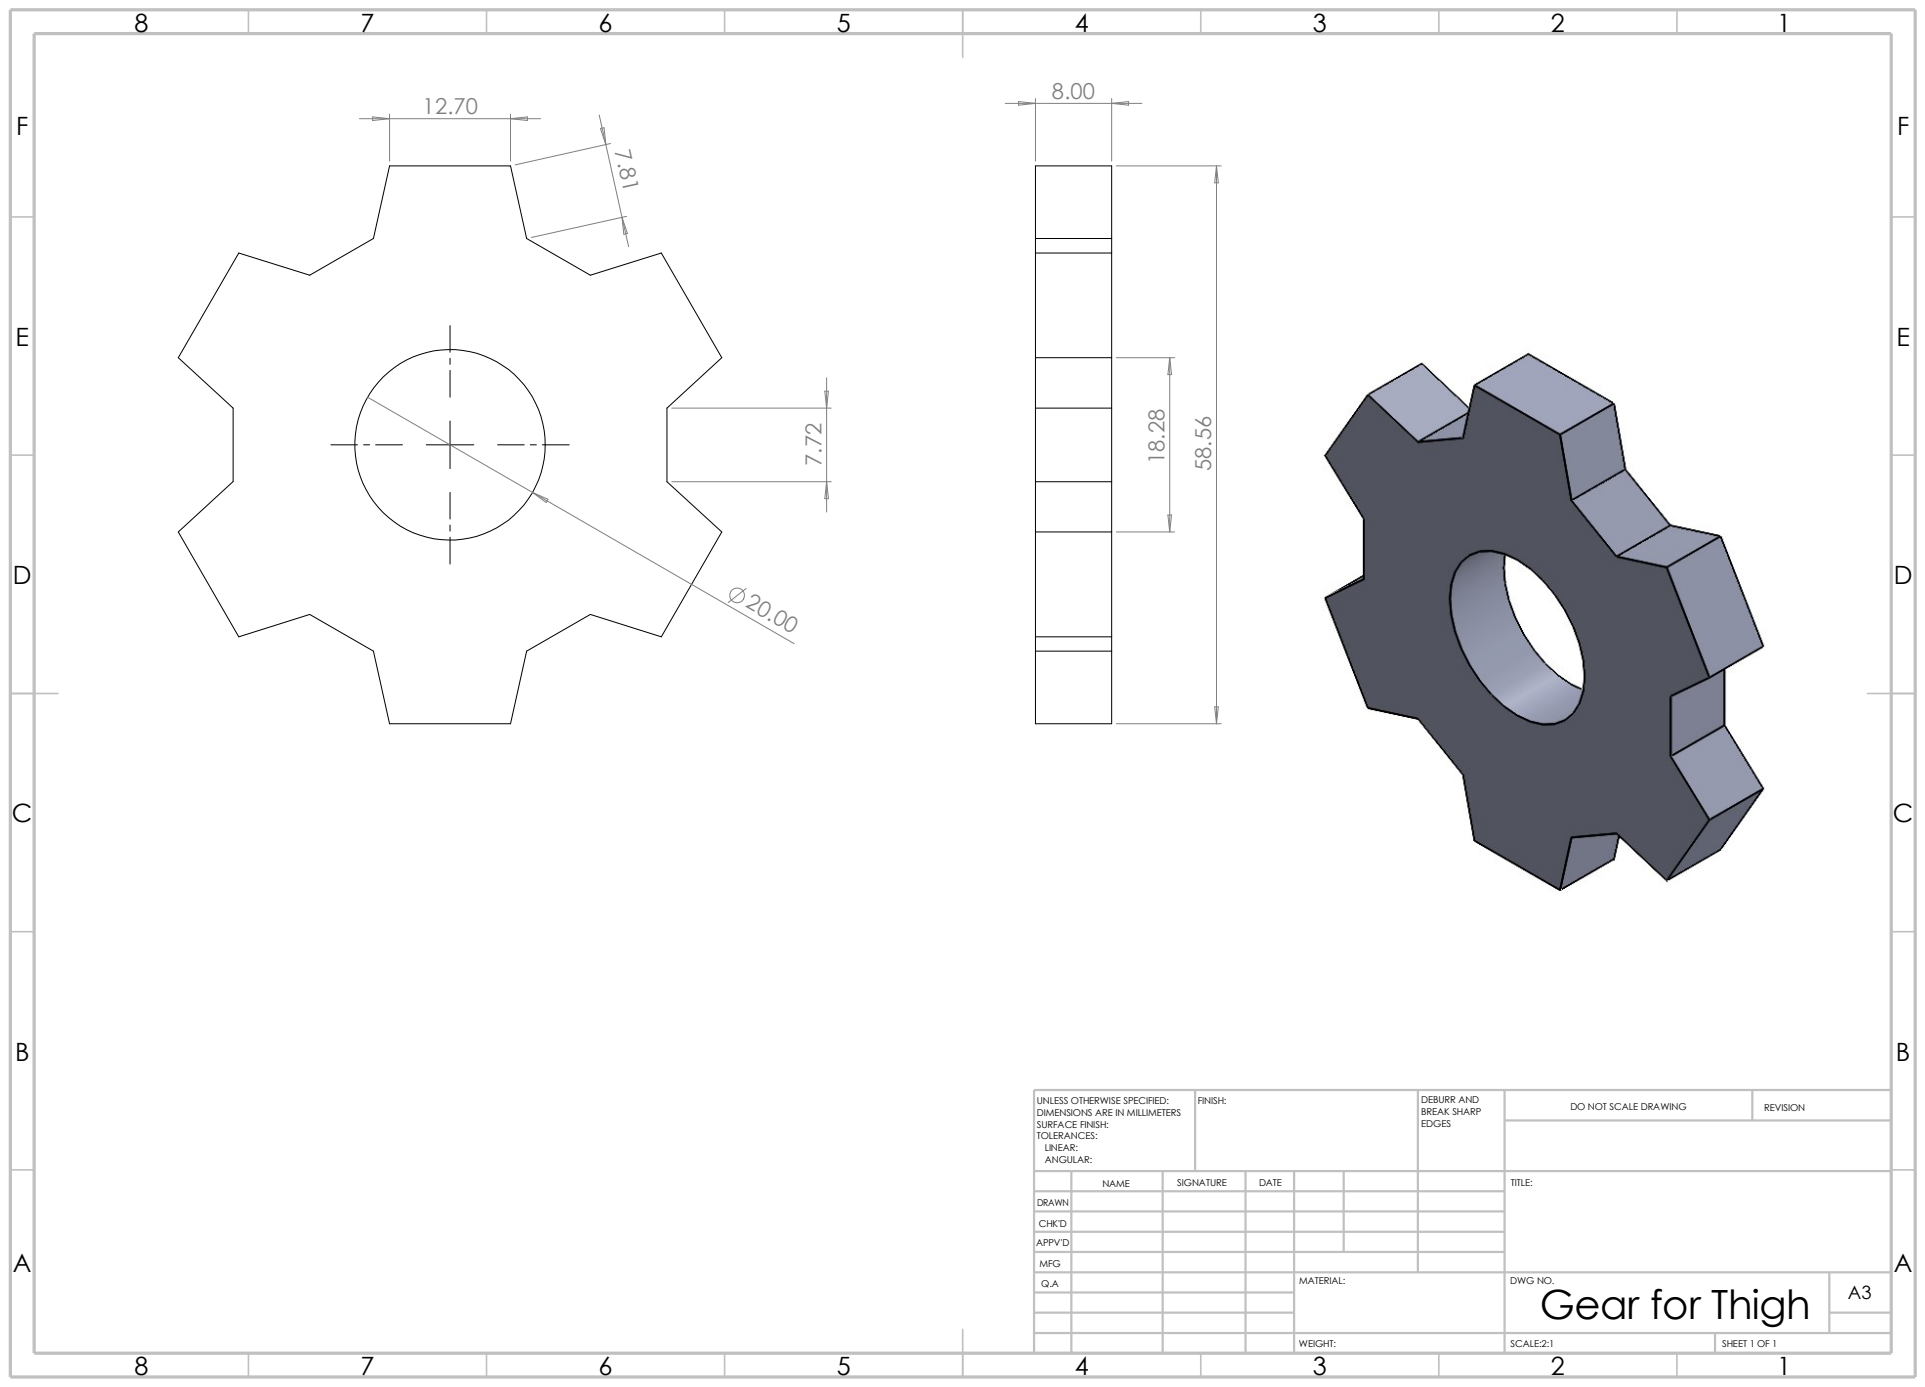
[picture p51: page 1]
SCALE:2:1; REVISION; SHEET 1 OF 1; WEIGHT:; EDGES; UNLESS OTHERWISE SPECIFIED:; FINISH:; DEBURR AND BREAK SHARP

Gear for Thigh ⁵⁸.56

DIMENSIONS ARE IN MILLIMETERS
SURFACE FINISH:
TOLERANCES:
LINEAR:
ANGULAR:

DO NOT SCALE DRAWING

NAME | SIGNATURE | DATE | | | | TITLE:

DRAWN
CHK'D
APPV'D

MFG
Q.A | | | | MATERIAL: | DWG NO. | A3

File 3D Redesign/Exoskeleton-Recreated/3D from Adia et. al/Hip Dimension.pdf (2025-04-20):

E E

F F

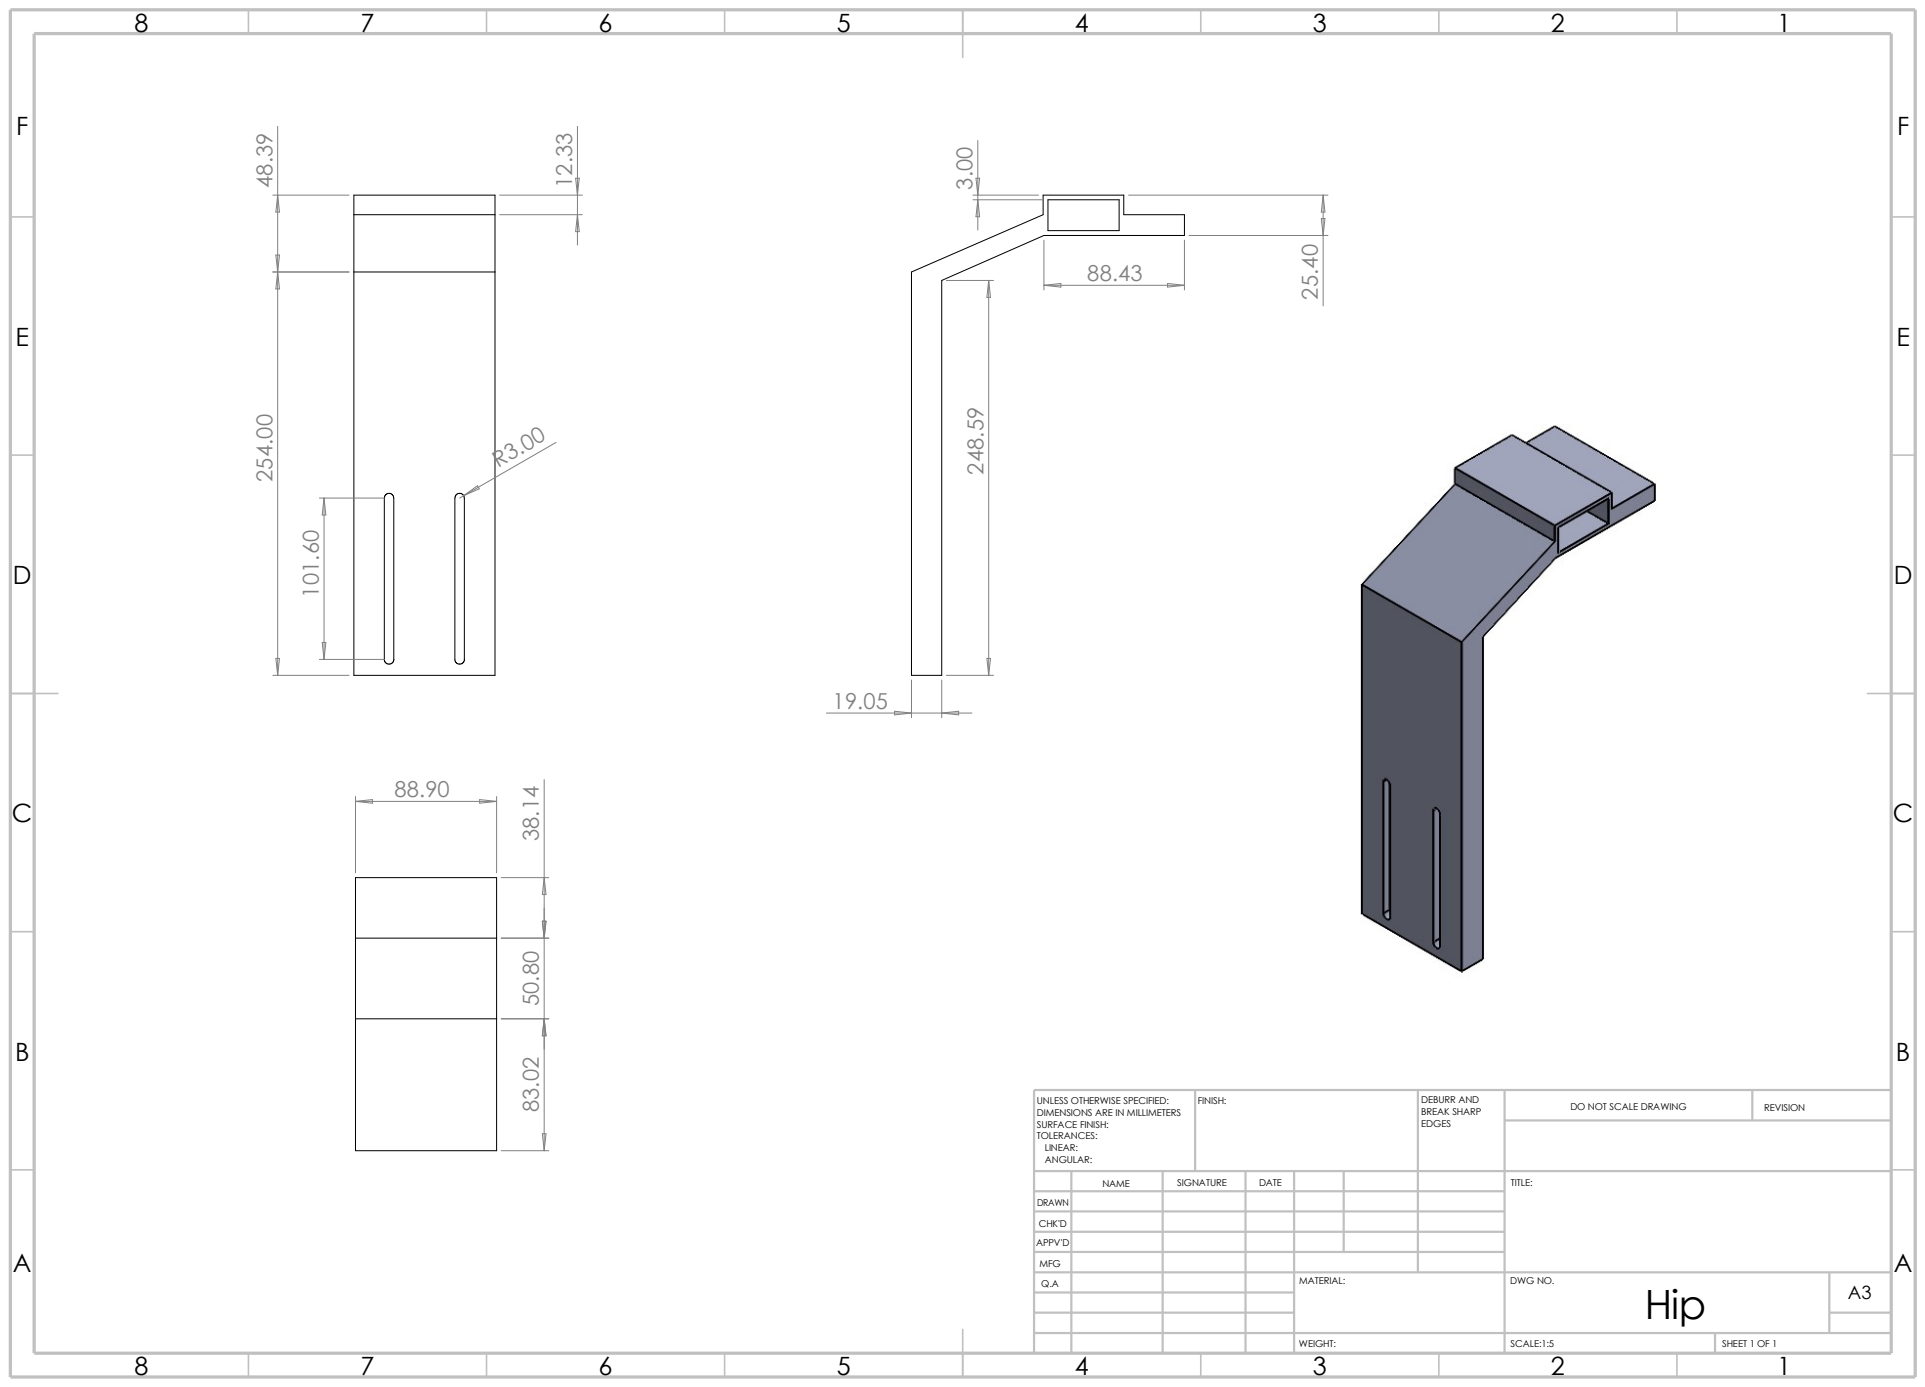
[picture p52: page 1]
WEIGHT:; SCALE:1:5; SHEET 1 OF 1; REVISION; FINISH:; EDGES; DEBURR AND BREAK SHARP; Hip ³⁸.14 88.90

DO NOT SCALE DRAWING UNLESS OTHERWISE SPECIFIED:
DIMENSIONS ARE IN MILLIMETERS
SURFACE FINISH:
TOLERANCES:
LINEAR:
ANGULAR:

NAME | SIGNATURE | DATE | | | | TITLE:

DRAWN
CHK'D
APPV'D
Q.A | | | | MATERIAL: | DWG NO. | A3

MFG

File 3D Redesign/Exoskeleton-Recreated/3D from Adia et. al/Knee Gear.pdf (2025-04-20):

E E

F F

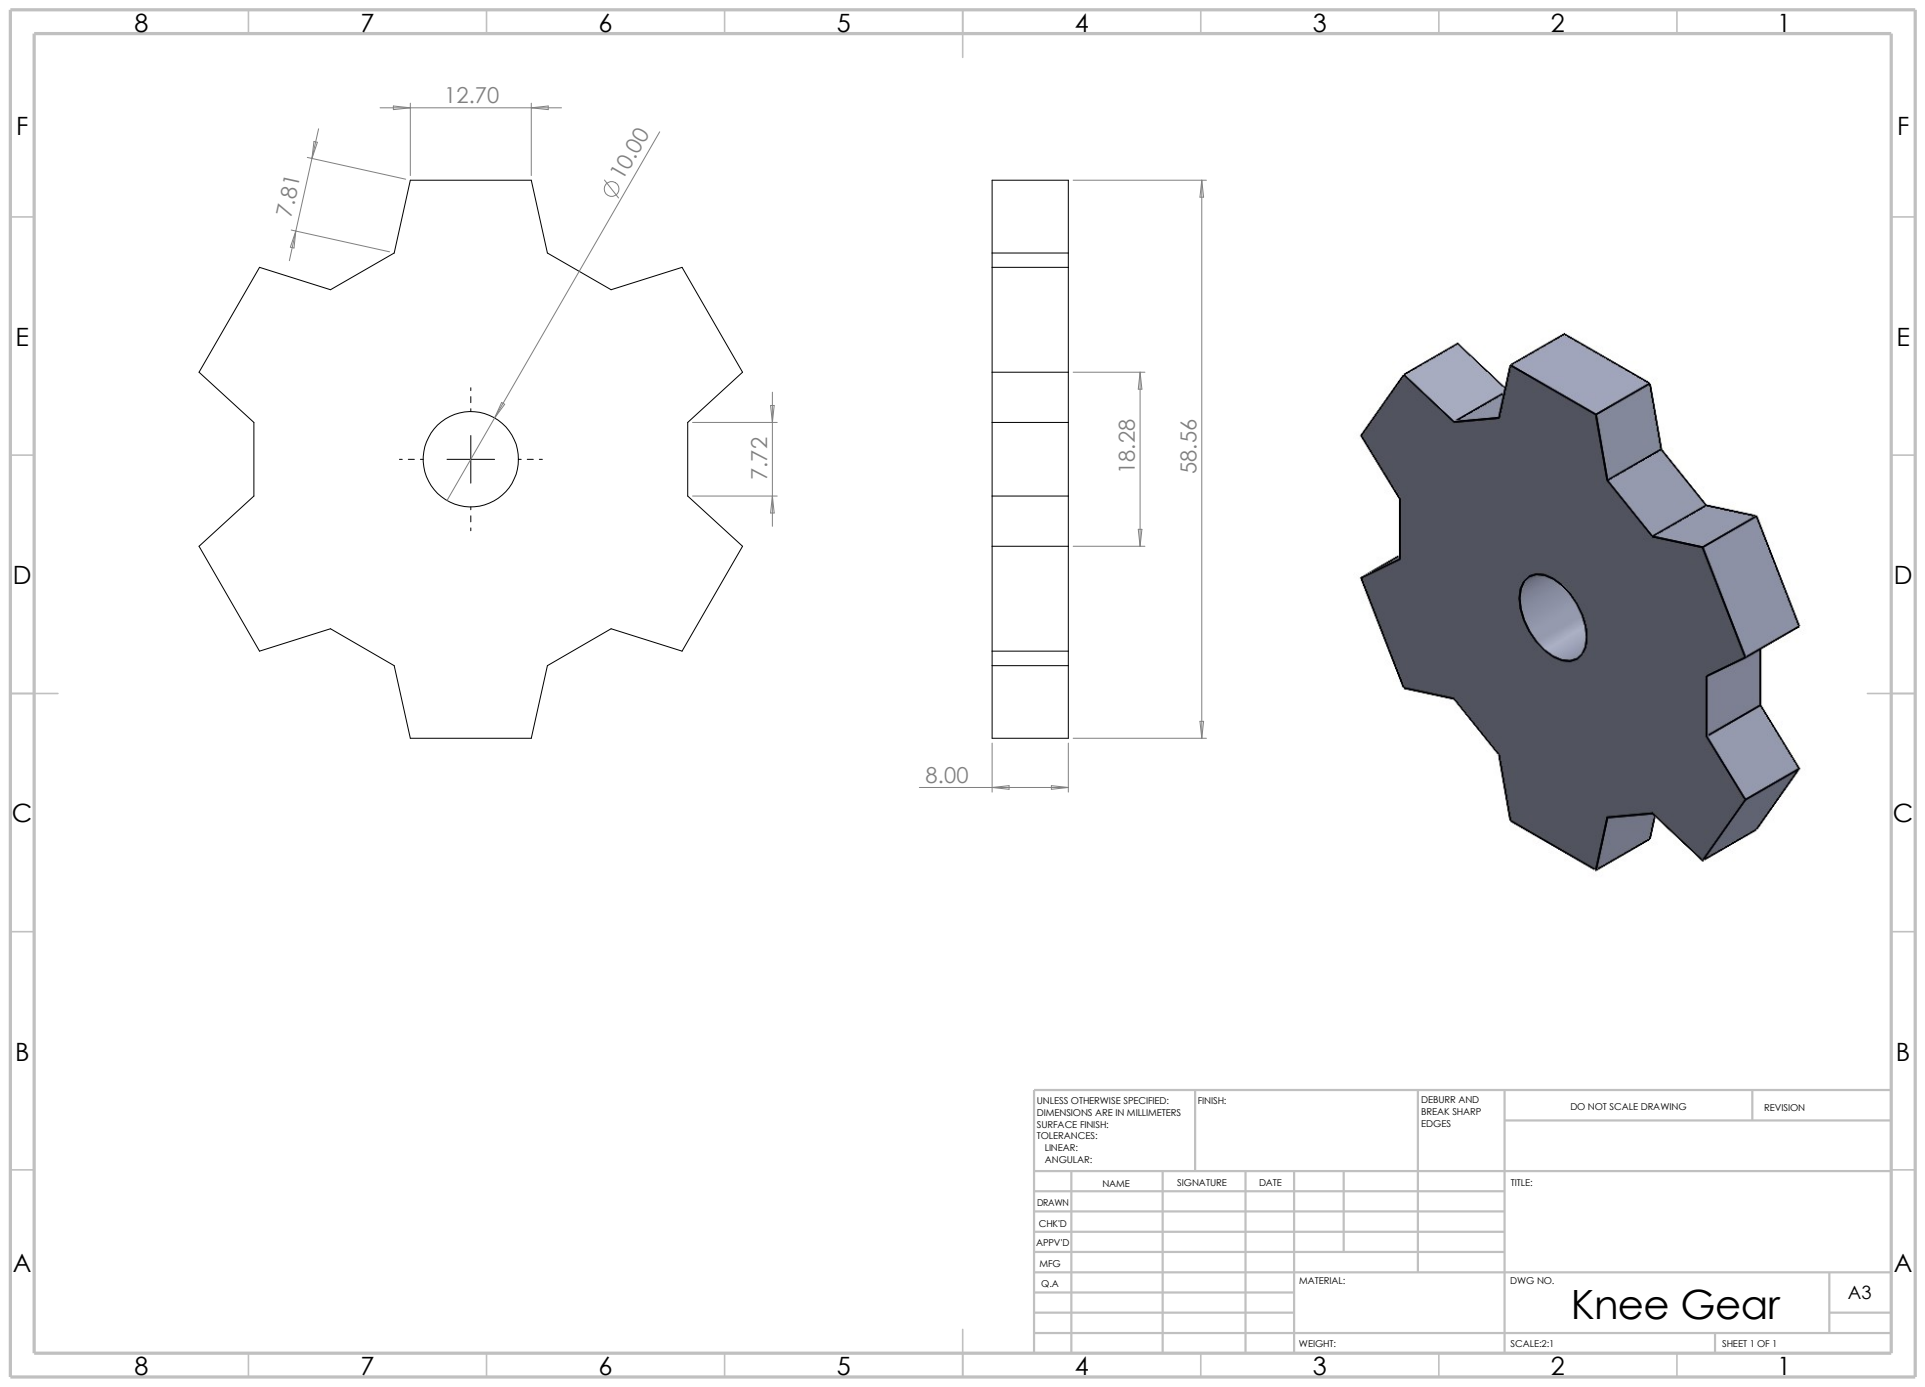
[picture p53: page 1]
SHEET 1 OF 1; WEIGHT:; SCALE:2:1; DO NOT SCALE DRAWING; REVISION; FINISH:; EDGES; DEBURR AND BREAK SHARP

UNLESS OTHERWISE SPECIFIED:
DIMENSIONS ARE IN MILLIMETERS
SURFACE FINISH:
TOLERANCES:
LINEAR:
ANGULAR:

NAME | SIGNATURE | DATE | | | | TITLE:

DRAWN
CHK'D
APPV'D
Q.A | | | | MATERIAL: | DWG NO. Knee Gear | A3

MFG

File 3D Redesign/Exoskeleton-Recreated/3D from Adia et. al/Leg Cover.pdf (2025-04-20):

12.70

E E

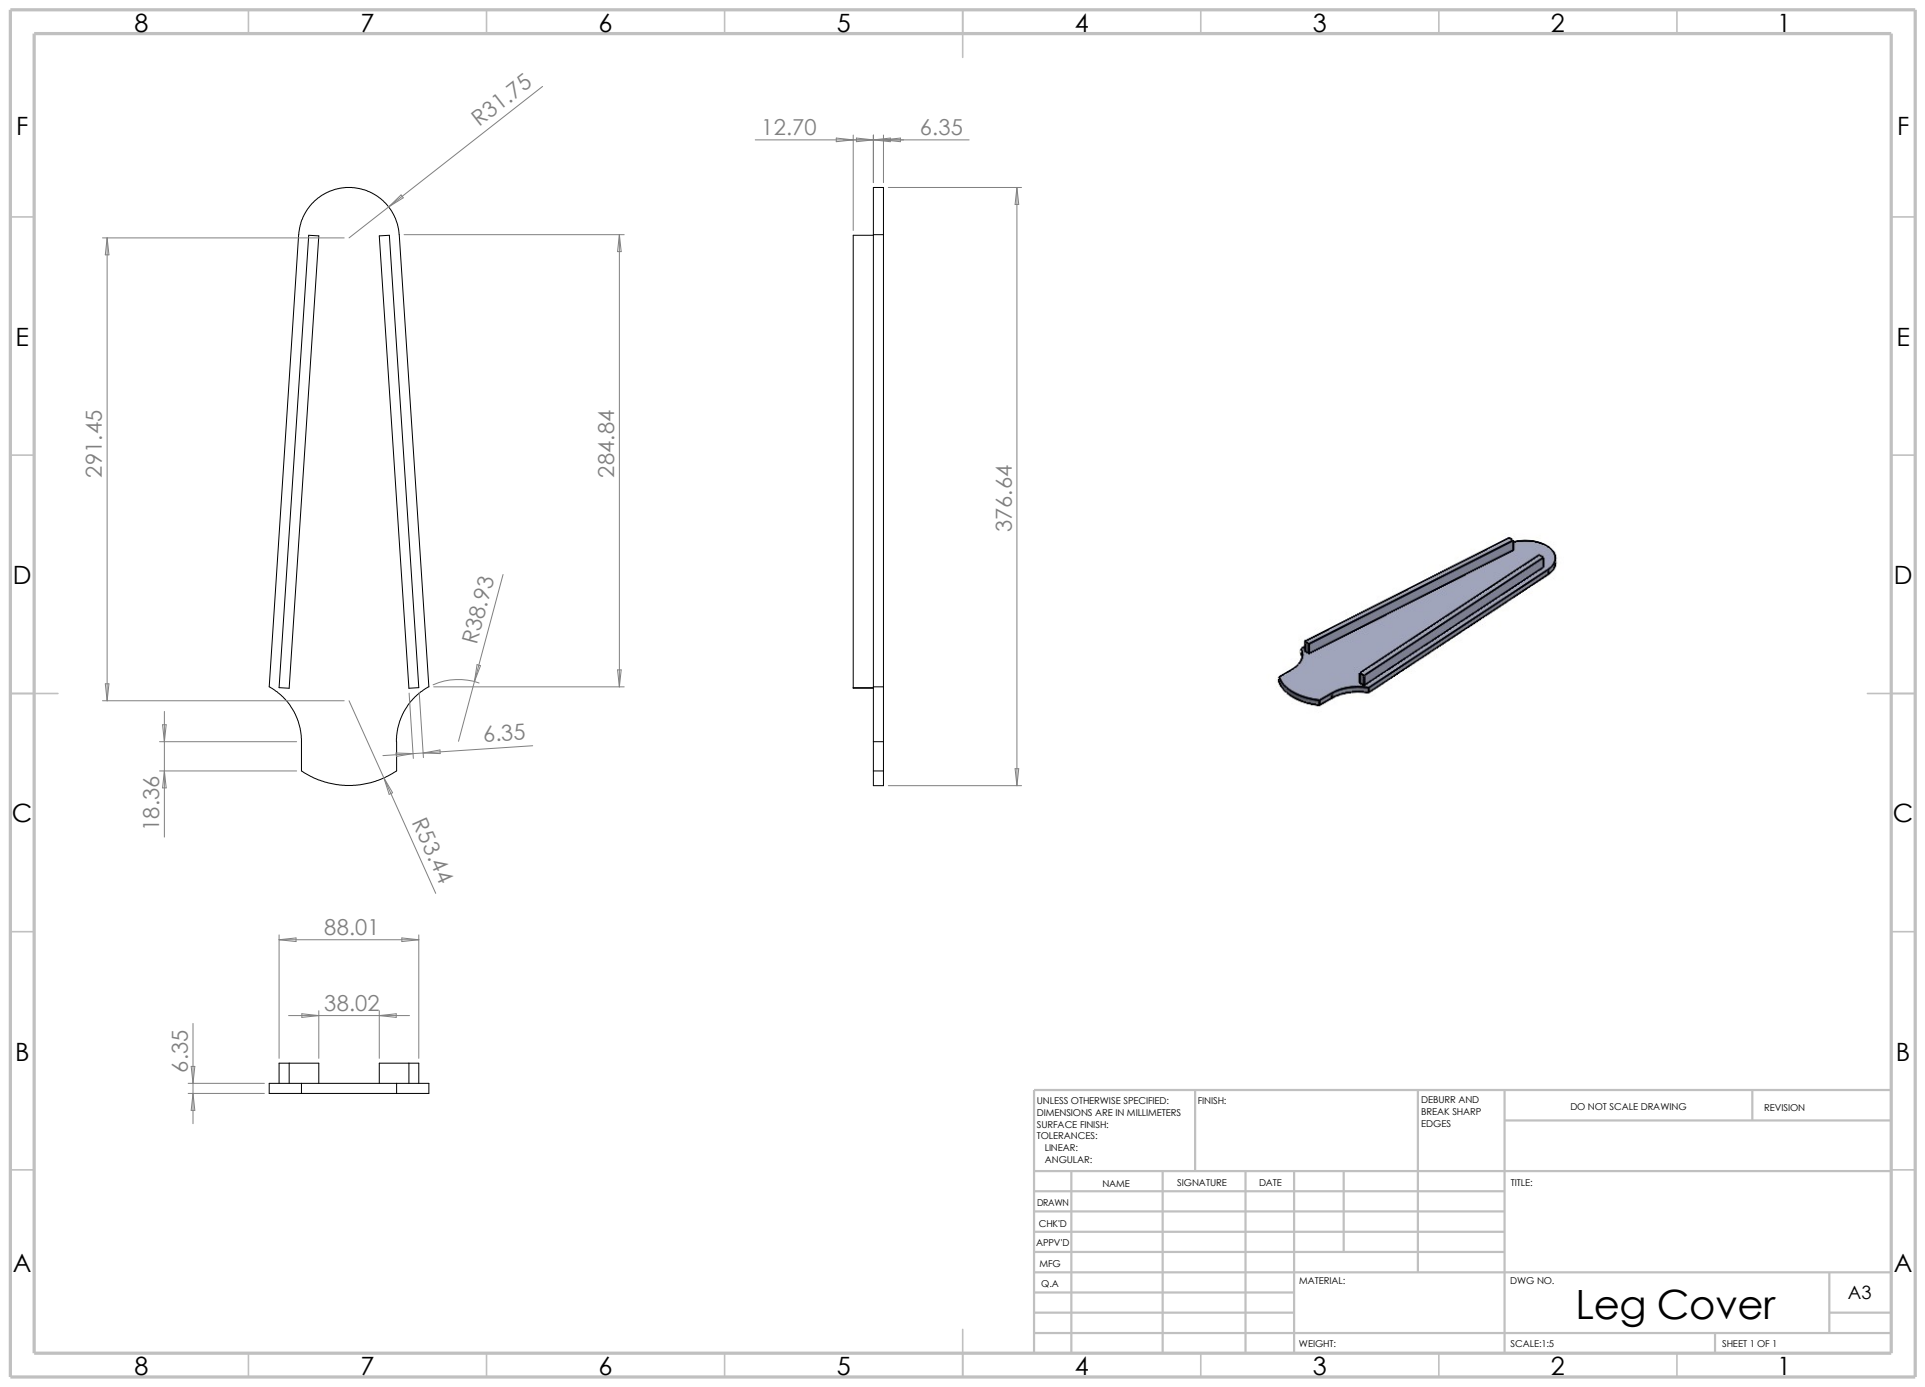
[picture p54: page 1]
WEIGHT:; SCALE:1:5; SHEET 1 OF 1; REVISION; FINISH:; EDGES; DEBURR AND BREAK SHARP

DO NOT SCALE DRAWING UNLESS OTHERWISE SPECIFIED:
DIMENSIONS ARE IN MILLIMETERS
SURFACE FINISH:
TOLERANCES:
LINEAR:
ANGULAR:

NAME | SIGNATURE | DATE | | | | TITLE:

DRAWN
CHK'D
APPV'D
Q.A | | | | MATERIAL: | DWG NO. Leg Cover | A3

MFG

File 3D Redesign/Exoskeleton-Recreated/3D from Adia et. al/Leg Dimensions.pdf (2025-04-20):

E E

F F

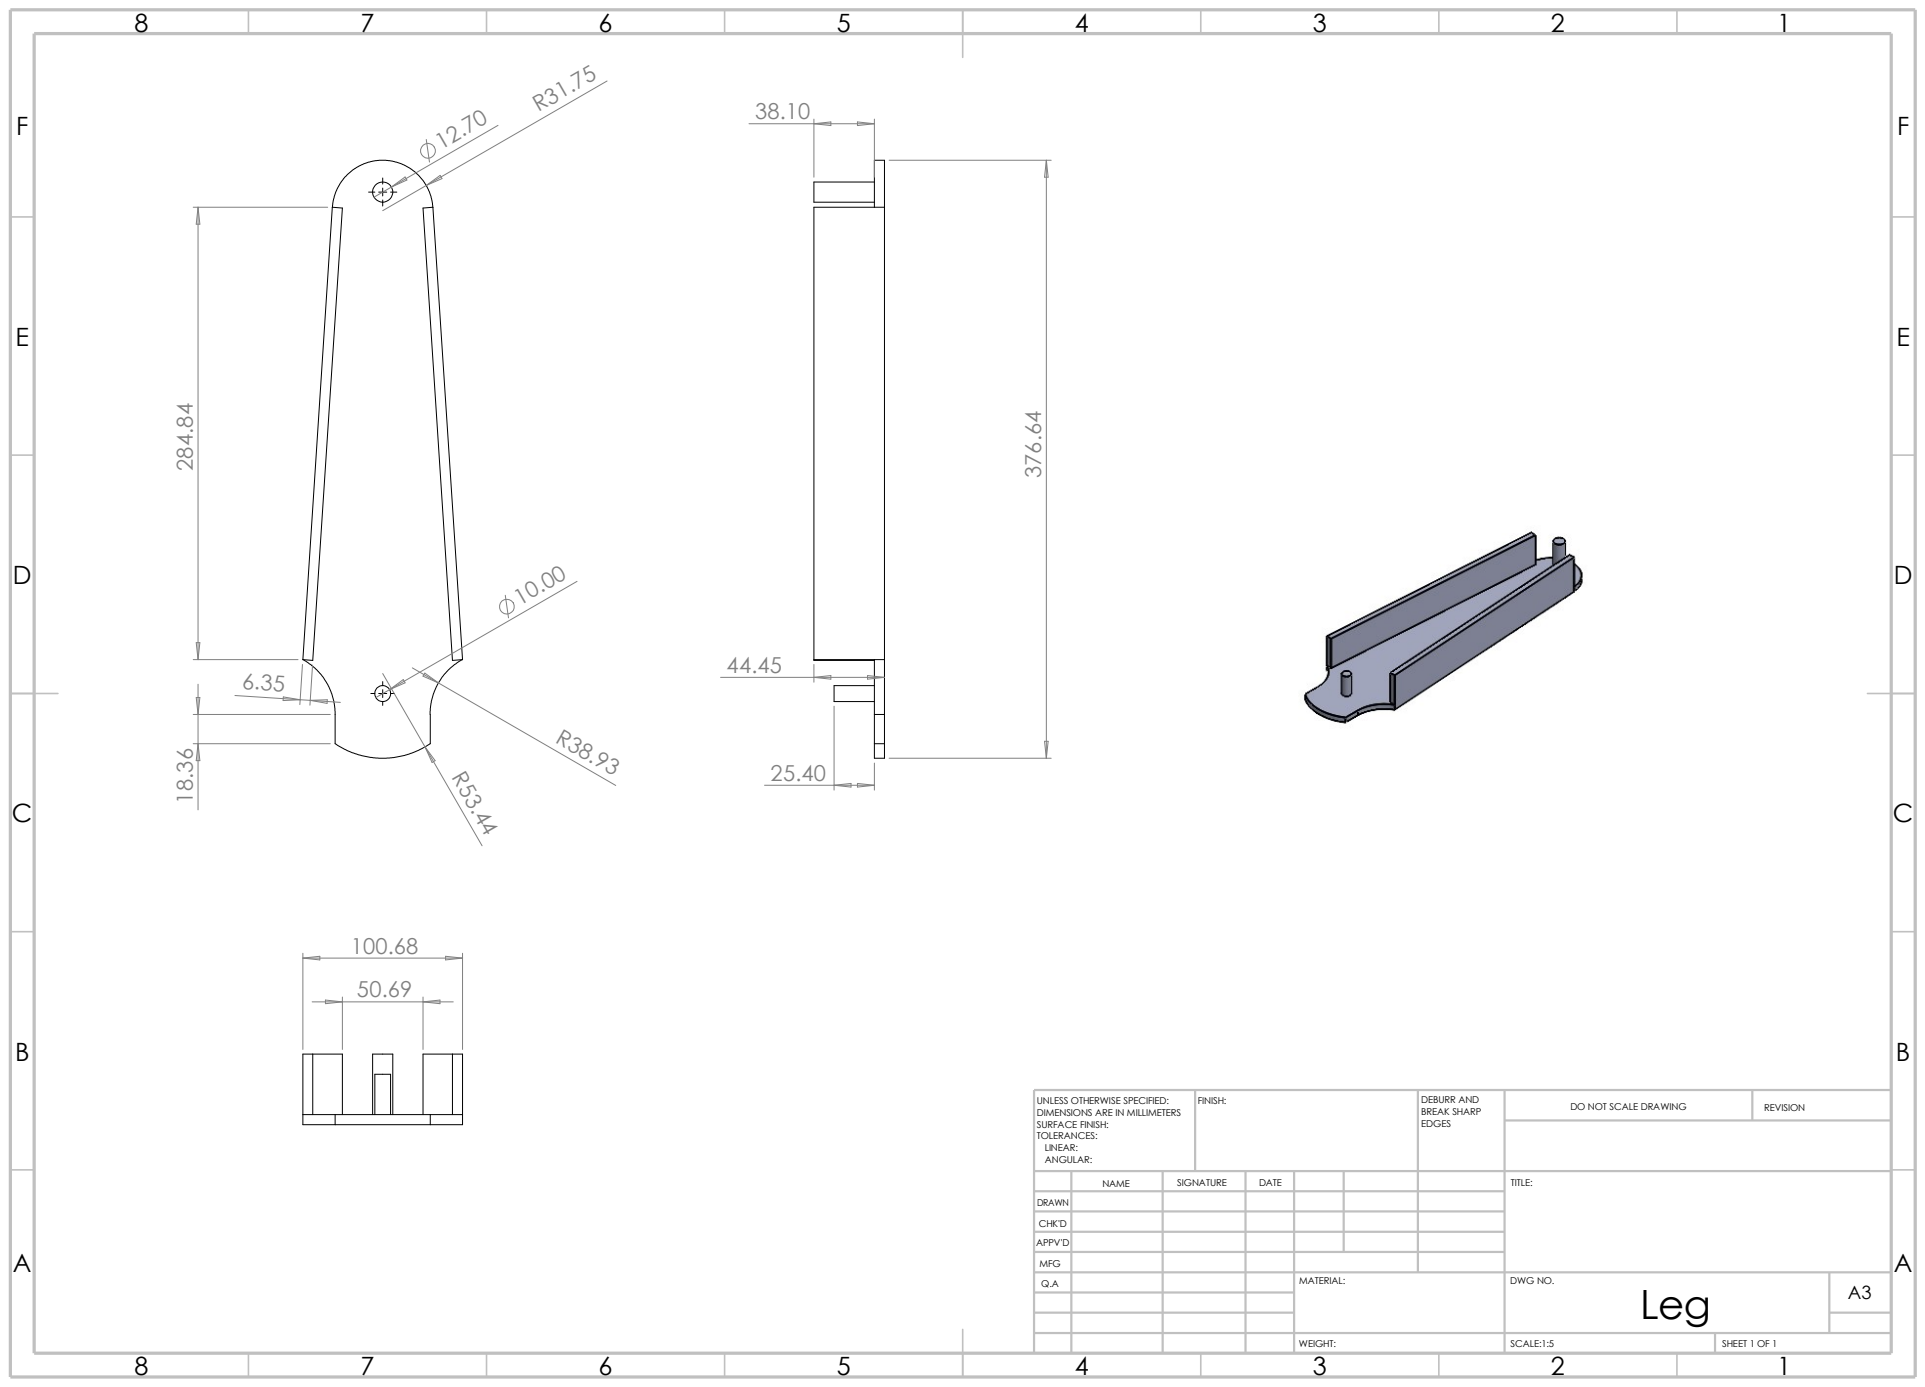
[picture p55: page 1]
SHEET 1 OF 1; WEIGHT:; SCALE:1:5; DO NOT SCALE DRAWING; REVISION; FINISH:; EDGES; DEBURR AND BREAK SHARP

UNLESS OTHERWISE SPECIFIED:
DIMENSIONS ARE IN MILLIMETERS
SURFACE FINISH:
TOLERANCES:
LINEAR:
ANGULAR:

NAME | SIGNATURE | DATE | | | | TITLE:

DRAWN
CHK'D
APPV'D
Q.A | | | | MATERIAL: | DWG NO. Leg | A3

MFG

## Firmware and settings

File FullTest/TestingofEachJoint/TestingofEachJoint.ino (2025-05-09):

#include <Wire.h>
#include <MPU6050.h>
#include <LiquidCrystal_I2C.h>

// I2C Multiplexer & LCD
#define PCA9548A_ADDRESS 0x70
LiquidCrystal_I2C lcd(0x27, 16, 2);

// Motor control pins
#define MOTOR1_PWM 6
#define MOTOR1_DIR 7
#define MOTOR2_PWM 8
#define MOTOR2_DIR 9
#define MOTOR3_PWM 10
#define MOTOR3_DIR 11
#define MOTOR4_PWM 12
#define MOTOR4_DIR 13

// Potentiometer pins
#define POT1 A0
#define POT2 A1
#define POT3 A2
#define POT4 A3

// Button pins
#define RESET_BUTTON 2
#define PAGE_BUTTON 3
#define SPEED_UP_BUTTON 4
#define SPEED_DOWN_BUTTON 5

#define POT_HYSTERESIS 5
const unsigned long THRESHOLD_DELAY = 500; // Adjust this value for the delay in milliseconds

float potResetAngles[4] = {170.0, 170.0, 170.0, 170.0};
float potEndHigh[4] = {255.0, 240.0, 240.0, 240.0};
float potEndLow[4] = {170.0, 145.0, 170.0, 145.0};

// MPU Thresholds
float mpuThresholds[4] = {6.0, 6.0, 6.0, 6.0};

#define MPU1_CHANNEL 0
#define MPU2_CHANNEL 2
#define MPU3_CHANNEL 1
#define MPU4_CHANNEL 3

MPU6050 mpu1, mpu2, mpu3, mpu4;

bool motorRunning[4] = {false, false, false, false};
bool reachedHigh[4] = {false, false, false, false};
unsigned long lastThresholdTime[4] = {0, 0, 0, 0};

int pwmPins[4] = {MOTOR1_PWM, MOTOR2_PWM, MOTOR3_PWM, MOTOR4_PWM};
int dirPins[4] = {MOTOR1_DIR, MOTOR2_DIR, MOTOR3_DIR, MOTOR4_DIR};
int potPins[4] = {POT1, POT2, POT3, POT4};
float potAngles[4] = {0, 0, 0, 0};
float accelY[4] = {0, 0, 0, 0};

byte currentPage = 0;
unsigned long lastButtonPress = 0;
const unsigned long DEBOUNCE_DELAY = 50;
int MOTOR_SPEED = 30;
const int SPEED_INCREMENT = 1;
const int MIN_SPEED = 0;
const int MAX_SPEED = 255;

enum State { WAIT_FORWARD, FORWARD, WAIT_REVERSE, REVERSE };
State currentState[4] = {WAIT_FORWARD, WAIT_FORWARD, WAIT_FORWARD, WAIT_FORWARD};

void selectI2CChannel(uint8_t channel) {
  Wire.beginTransmission(PCA9548A_ADDRESS);
  Wire.write(1 << channel);
  Wire.endTransmission();
  delay(10);
}

void setupMPU(MPU6050 &mpu, uint8_t channel) {
  selectI2CChannel(channel);
  mpu.initialize();
  if (mpu.testConnection()) {
    Serial.print("MPU ");
    Serial.print(channel);
    Serial.println(" connected.");
  } else {
    Serial.print("MPU ");
    Serial.print(channel);
    Serial.println(" FAILED!");
  }
}

float getAccelY(MPU6050 &mpu, uint8_t channel) {
  selectI2CChannel(channel);
  int16_t ax, ay, az;
  mpu.getMotion6(&ax, &ay, &az, nullptr, nullptr, nullptr);
  return (float)ay / 16384.0 * 9.81;
}

float readPotentiometerAngle(int pin) {
  int val = analogRead(pin);
  return map(val, 0, 1023, 0, 300);
}

void startMotor(int index, bool forward) {
  digitalWrite(dirPins[index], forward ? HIGH : LOW);
  analogWrite(pwmPins[index], MOTOR_SPEED);
  motorRunning[index] = true;
  Serial.print("Motor ");
  Serial.print(index + 1);
  Serial.println(forward ? " STARTED FORWARD" : " STARTED REVERSE");
}

void stopMotor(int index) {
  analogWrite(pwmPins[index], 0);
  motorRunning[index] = false;
  Serial.print("Motor ");
  Serial.print(index + 1);
  Serial.println(" STOPPED");
  lastThresholdTime[index] = millis(); // Record the time when the motor stopped
}

void displayLCD() {
  lcd.clear();
  switch (currentPage) {
    case 0:
      lcd.setCursor(0, 0);
      lcd.print("P1:");
      lcd.print((int)potAngles[0]);
      lcd.print(" M1:");
      lcd.print(accelY[0], 1);
      lcd.setCursor(0, 1);
      lcd.print("P2:");
      lcd.print((int)potAngles[1]);
      lcd.print(" M2:");
      lcd.print(accelY[1], 1);
      break;
    case 1:
      lcd.setCursor(0, 0);
      lcd.print("P3:");
      lcd.print((int)potAngles[2]);
      lcd.print(" M3:");
      lcd.print(accelY[2], 1);
      lcd.setCursor(0, 1);
      lcd.print("P4:");
      lcd.print((int)potAngles[3]);
      lcd.print(" M4:");
      lcd.print(accelY[3], 1);
      break;
    case 2:
      lcd.setCursor(0, 0);
      lcd.print("Speed:");
      lcd.print(MOTOR_SPEED);
      break;
  }
}

void resetToAngle() {
  for (int i = 0; i < 4; i++) {
    float targetAngle = potResetAngles[i];
    float currentAngle = potAngles[i];

    // Determine direction based on motor position and target
    bool forward;
    if (i == 0 || i == 2) { // M1 and M3: Move towards higher angle
      forward = (currentAngle < targetAngle);
    } else { // M2 and M4: Move towards lower angle
      forward = (currentAngle > targetAngle);
    }

    // Start the motor
    startMotor(i, forward);
    motorRunning[i] = true; // Set the motorRunning flag

    // Set the state to FORWARD or REVERSE depending on the direction
    currentState[i] = forward ? FORWARD : REVERSE;
  }
  // Add this section to stop the motors
  bool allStopped = false;
  while (!allStopped) {
    allStopped = true; // Assume all are stopped until proven otherwise
    for (int i = 0; i < 4; i++) {
      float currentAngle = readPotentiometerAngle(potPins[i]); // Re-read pot angle
      if (motorRunning[i]) { //if motor is still running
        if (abs(currentAngle - potResetAngles[i]) <= 5) { // Within 5 degrees
          stopMotor(i);
        }
        else{
          allStopped = false;
        }
      }
    }
    delay(10); // Short delay to prevent overwhelming the processor
  }
  for(int i=0; i<4; i++){
    currentState[i] = WAIT_FORWARD;
  }
}


void handlePageButton() {
  if (digitalRead(PAGE_BUTTON) == LOW && (millis() - lastButtonPress > DEBOUNCE_DELAY)) {
    currentPage++;
    if (currentPage > 2) {
      currentPage = 0;
    }
    displayLCD();
    lastButtonPress = millis();
  }
}

void adjustSpeed(int change) {
  if (millis() - lastButtonPress > DEBOUNCE_DELAY) {
    MOTOR_SPEED += change;
    if (MOTOR_SPEED > MAX_SPEED) {
      MOTOR_SPEED = MAX_SPEED;
    } else if (MOTOR_SPEED < MIN_SPEED) {
      MOTOR_SPEED = MIN_SPEED;
    }
    lastButtonPress = millis();

    // Update the speed of any currently running motors
    for (int i = 0; i < 4; i++) {
      if (motorRunning[i]) {
        analogWrite(pwmPins[i], MOTOR_SPEED);
      }
    }
    displayLCD();
  }
}

void setup() {
  Serial.begin(115200);
  Wire.begin();
  lcd.init();
  lcd.backlight();
  lcd.setCursor(0, 0);
  lcd.print("Initializing...");

  pinMode(RESET_BUTTON, INPUT_PULLUP);
  pinMode(PAGE_BUTTON, INPUT_PULLUP);
  pinMode(SPEED_UP_BUTTON, INPUT_PULLUP);
  pinMode(SPEED_DOWN_BUTTON, INPUT_PULLUP);

  for (int i = 0; i < 4; i++) {
    pinMode(pwmPins[i], OUTPUT);
    pinMode(dirPins[i], OUTPUT);
  }

  setupMPU(mpu1, MPU1_CHANNEL);
  setupMPU(mpu2, MPU2_CHANNEL);
  setupMPU(mpu3, MPU3_CHANNEL);
  setupMPU(mpu4, MPU4_CHANNEL);

  lcd.clear();
  lcd.print("System Ready");
  delay(1000);
}

void loop() {
  MPU6050* mpus[4] = {&mpu1, &mpu2, &mpu3, &mpu4};
  uint8_t channels[4] = {MPU1_CHANNEL, MPU2_CHANNEL, MPU3_CHANNEL, MPU4_CHANNEL};

  for (int i = 0; i < 4; i++) {
    potAngles[i] = readPotentiometerAngle(potPins[i]);
    accelY[i] = getAccelY(*mpus[i], channels[i]);
  }

  if (digitalRead(RESET_BUTTON) == LOW) {
    resetToAngle();
    delay(300);
    return;
  }

  handlePageButton();
  if (digitalRead(SPEED_UP_BUTTON) == LOW) {
    adjustSpeed(SPEED_INCREMENT);
  }
  if (digitalRead(SPEED_DOWN_BUTTON) == LOW) {
    adjustSpeed(-SPEED_INCREMENT);
  }

  for (int i = 0; i < 4; i++) {
    switch (currentState[i]) {
      case WAIT_FORWARD:
        if (millis() - lastThresholdTime[i] >= THRESHOLD_DELAY) {
          if (i == 0 || i == 2) { // MPU 1 & 3: Positive threshold for forward
            if (accelY[i] > mpuThresholds[i]) {
              startMotor(i, true);
              currentState[i] = FORWARD;
            } else if (accelY[i] < -mpuThresholds[i]) {
              startMotor(i, false);
              currentState[i] = REVERSE;
            }
          } else { // MPU 2 & 4: Positive threshold for reverse
            if (accelY[i] > mpuThresholds[i]) {
              startMotor(i, false);
              currentState[i] = REVERSE;
            } else if (accelY[i] < -mpuThresholds[i]) {
              startMotor(i, true);
              currentState[i] = FORWARD;
            }
          }
        }
        break;
      case FORWARD:
        if (potAngles[i] >= potEndHigh[i] - POT_HYSTERESIS) {
          stopMotor(i);
          currentState[i] = WAIT_REVERSE;
          reachedHigh[i] = true;
        }
        break;
      case WAIT_REVERSE:
        if (millis() - lastThresholdTime[i] >= THRESHOLD_DELAY) {
          if (i == 0 || i == 2) { // MPU 1 & 3: Negative threshold for reverse
            if (accelY[i] < -mpuThresholds[i]) {
              startMotor(i, false);
              currentState[i] = REVERSE;
            } else if (accelY[i] > mpuThresholds[i]) {
              startMotor(i, true);
              currentState[i] = FORWARD;
            }
          } else { // MPU 2 & 4: Negative threshold for forward
            if (accelY[i] < -mpuThresholds[i]) {
              startMotor(i, true);
              currentState[i] = FORWARD;
            } else if (accelY[i] > mpuThresholds[i]) {
              startMotor(i, false);
              currentState[i] = REVERSE;
            }
          }
        }
        break;
      case REVERSE:
        if (potAngles[i] <= potEndLow[i] + POT_HYSTERESIS) {
          stopMotor(i);
          currentState[i] = WAIT_FORWARD;
          reachedHigh[i] = false; // Reset reachedHigh when going back
        }
        break;
      delay(53);
    }
  }

  displayLCD();
  delay(50); // Reduced delay for smoother operation
}

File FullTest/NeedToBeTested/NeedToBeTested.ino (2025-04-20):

#include <Wire.h>
#include <MPU6050.h>

#define PCA9548A_ADDRESS 0x70   // I2C address of PCA9548A
#define ACCEL_THRESHOLD 500     // Threshold in raw accel units
#define POT_PIN A0              // Analog pin for potentiometer

// Motor control pins for 4 motors
#define MOTOR1_PWM 5
#define MOTOR1_DIR 4
#define MOTOR2_PWM 6
#define MOTOR2_DIR 7
#define MOTOR3_PWM 9
#define MOTOR3_DIR 8
#define MOTOR4_PWM 10
#define MOTOR4_DIR 11

// Channels for each MPU
#define MPU1_CHANNEL 0
#define MPU2_CHANNEL 1
#define MPU3_CHANNEL 2
#define MPU4_CHANNEL 3

// MPU instances
MPU6050 mpu1;
MPU6050 mpu2;
MPU6050 mpu3;
MPU6050 mpu4;

// Motor state
bool motorRunning[4] = {false, false, false, false};
bool motorDirectionForward[4] = {true, true, true, true};
const float POT_RESET_ANGLE = 200.0; // Angle to stop motor

void selectI2CChannel(uint8_t channel) {
  Wire.beginTransmission(PCA9548A_ADDRESS);
  Wire.write(1 << channel);
  Wire.endTransmission();
  delay(10);
}

void setupMPU(MPU6050 &mpu, uint8_t channel) {
  selectI2CChannel(channel);
  mpu.initialize();
  if (mpu.testConnection()) {
    Serial.print("MPU6050 on channel ");
    Serial.print(channel);
    Serial.println(" connected successfully.");
  } else {
    Serial.print("MPU6050 on channel ");
    Serial.print(channel);
    Serial.println(" connection failed!");
  }
}

float getAccelX(MPU6050 &mpu, uint8_t channel) {
  selectI2CChannel(channel);
  int16_t ax, ay, az;
  mpu.getMotion6(&ax, &ay, &az, nullptr, nullptr, nullptr);
  return (float)ax / 16384.0 * 9.81;
}

float readPotentiometerAngle() {
  int potValue = analogRead(POT_PIN);
  float angle = map(potValue, 0, 1023, 0, 300);
  return angle;
}

void startMotor(int index, int pwmPin, int dirPin, bool forward) {
  digitalWrite(dirPin, forward ? HIGH : LOW);
  analogWrite(pwmPin, 200);
  motorRunning[index] = true;
  motorDirectionForward[index] = forward;
  Serial.print("Motor "); Serial.print(index + 1);
  Serial.println(forward ? " STARTED FORWARD." : " STARTED REVERSE.");
}

void stopMotor(int index, int pwmPin) {
  analogWrite(pwmPin, 0);
  motorRunning[index] = false;
  Serial.print("Motor "); Serial.print(index + 1);
  Serial.println(" STOPPED by potentiometer.");
}

void checkThresholds() {
  float accelX[4];
  MPU6050* mpus[4] = {&mpu1, &mpu2, &mpu3, &mpu4};
  uint8_t channels[4] = {MPU1_CHANNEL, MPU2_CHANNEL, MPU3_CHANNEL, MPU4_CHANNEL};
  int pwmPins[4] = {MOTOR1_PWM, MOTOR2_PWM, MOTOR3_PWM, MOTOR4_PWM};
  int dirPins[4] = {MOTOR1_DIR, MOTOR2_DIR, MOTOR3_DIR, MOTOR4_DIR};

  for (int i = 0; i < 4; i++) {
    accelX[i] = getAccelX(*mpus[i], channels[i]);
    Serial.print("MPU"); Serial.print(i + 1); Serial.print(" Accel X: "); Serial.print(accelX[i]); Serial.print(" | ");
  }
  Serial.println();

  float scaled_threshold = ACCEL_THRESHOLD / 100.0;
  float final_threshold = 8.0;

  // Pair logic: MPU1 & MPU2, MPU3 & MPU4
  float avgAccelGroup1 = (accelX[0] + accelX[1]) / 2.0;
  float avgAccelGroup2 = (accelX[2] + accelX[3]) / 2.0;

  for (int i = 0; i < 2; i++) {
    if (!motorRunning[i]) {
      if (avgAccelGroup1 > final_threshold || abs(avgAccelGroup1) > scaled_threshold) {
        startMotor(i, pwmPins[i], dirPins[i], true);
      } else if (avgAccelGroup1 < -2.0) {
        startMotor(i, pwmPins[i], dirPins[i], false);
      }
    }
  }

  for (int i = 2; i < 4; i++) {
    if (!motorRunning[i]) {
      if (avgAccelGroup2 > final_threshold || abs(avgAccelGroup2) > scaled_threshold) {
        startMotor(i, pwmPins[i], dirPins[i], true);
      } else if (avgAccelGroup2 < -2.0) {
        startMotor(i, pwmPins[i], dirPins[i], false);
      }
    }
  }
}

void setup() {
  Serial.begin(115200);
  Wire.begin();

  pinMode(MOTOR1_PWM, OUTPUT);
  pinMode(MOTOR1_DIR, OUTPUT);
  pinMode(MOTOR2_PWM, OUTPUT);
  pinMode(MOTOR2_DIR, OUTPUT);
  pinMode(MOTOR3_PWM, OUTPUT);
  pinMode(MOTOR3_DIR, OUTPUT);
  pinMode(MOTOR4_PWM, OUTPUT);
  pinMode(MOTOR4_DIR, OUTPUT);

  Serial.println("Initializing MPU6050 sensors...");
  setupMPU(mpu1, MPU1_CHANNEL);
  setupMPU(mpu2, MPU2_CHANNEL);
  setupMPU(mpu3, MPU3_CHANNEL);
  setupMPU(mpu4, MPU4_CHANNEL);
  Serial.println("Sensors initialized.");
}

void loop() {
  float potAngle = readPotentiometerAngle();
  Serial.print("Potentiometer Angle: ");
  Serial.println(potAngle);

  checkThresholds();

  int pwmPins[4] = {MOTOR1_PWM, MOTOR2_PWM, MOTOR3_PWM, MOTOR4_PWM};

  for (int i = 0; i < 4; i++) {
    if (motorRunning[i] && potAngle >= POT_RESET_ANGLE) {
      stopMotor(i, pwmPins[i]);
    }
  }

  delay(2000);
}

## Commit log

2025-02-27 Create Foot with straps.SLDDRW
    [Foot with straps.SLDDRW]
2025-02-27 Create Foot with straps.SLDPRT
    [Foot with straps.SLDPRT]
2025-02-28 Uploaded Stage 1 of Cycloidal Drives
2025-03-01 Upload Cycloidal Drive and Organize Folders
    [Foot with straps.SLDPRT, Hip Joint.SLDPRT, Hip Mechanical Stop.SLDPRT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]
2025-03-03 Upload Foot Draft
    [Foot.SLDPRT, Hip Joint.SLDPRT, Hip Jointt.SLDPRT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]
2025-03-04 Update Leg Link.SLDPRT
    [Leg Link.SLDPRT]
2025-03-05 Update Cycloidal Drive and Exoskeleton Assembly
    [13isto1.SLDPRT, Cover.SLDPRT, Cycloidial GearBox.SLDASM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]
2025-03-13 Added Output Shaft. See V3.1
2025-03-13 Added Frames and Prototypes STEP and SLDPRT of Elx
2025-03-16 Adjusted based on Bearings Availability and 3D Print
2025-03-19 Redesign of the Objective 1
    [Extension 2_Default_sldprt.STEP, Extension for hip part_Default_sldprt.STEP, Feet Gear_Default_sldprt.STEP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]
2025-03-24 Added Foot Assembly
    [Foot Assembly.SLDASM, Foot Joint Assembly.SLDASM, Foot Joint.SLDPRT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]
2025-04-05 Stress Analysis on foot
    [Foot Assembly.SLDASM]
2025-04-05 Left and Right Foot Assembly (ACP)
    [Foot Assembly R.SLDASM, Foot Joint Assembly.SLDASM, Foot Joint.SLDPRT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]
2025-04-05 Deleted Files
    [Foot Assembly.SLDASM, Foot Joint Assembly.SLDASM, Foot Joint.SLDPRT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]
2025-04-05 Foot Left and Right (Aluminum)
    [Foot Left.SLDPRT, Foot Right.SLDPRT]
2025-04-07 Uploaded Exoskeleton Assembly V2
    [12 tooth for coupling.SLDPRT, Bushing.SLDPRT, Cyclodial Gear Stage Two.SLDPRT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]
2025-04-07 Added Revisions on Gearbox v.3.1.1.
    [12 tooth for coupling.SLDPRT, 13isto1.STL, Cover.STL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]
2025-04-08 Created Exploded view and v4.0 of Cyclodial Gear
    [Cyclodial Gear Stage 2 rev a.SLDPRT, Cyclodial Gear rev a.SLDPRT, Cyclodial gearbox v.4.0 exploded view.SLDASM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]
2025-04-09 Revised v.4.0
    [Foot Left.SLDPRT]
2025-04-13 Converting sldprt from step files
    [Control Box.SLDPRT, Cyclodial Gearbox.SLDASM, Cyclodial gearbox v.4.0.SLDASM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]
2025-04-17 Included Computations for thw things
    [Leg Assembly.SLDDRW]
2025-04-20 Added Drawings as per consultation
    [Cyclodial gearbox v.4.0 exploded view.SLDASM, Cyclodial gearbox v.4.0 exploded view.SLDDRW, Foot Assembly R.SLDASM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]
2025-04-20 Created Assembly
    [Leg Part.SLDASM, Thigh Part.SLDASM]
2025-04-20 3D from Adia et al
    [Exoskeleton Assembly UTOG.SLDASM, Exoskeleton Assembly Very Utog.SLDASM, Exoskeleton Assembly'.SLDASM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]
2025-04-20 Create ~$Feet Gear.SLDPRT
2025-04-20 Checking of SOLIDWROSK
    [Adia Lower Body Exoskeleton.SLDASM]
2025-04-22 Revision of Drawings
    [Foot with Straps.SLDPRT, Hip Part.SLDASM, Leg Part.SLDASM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]
2025-05-26 Hip Part Assembly
    [Hip Part 2 Layer 1st and 2nd Layer.SLDPRT, Hip Part 2 Layer 3rd Layer.SLDPRT, Hip Part Assembly.SLDASM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]
